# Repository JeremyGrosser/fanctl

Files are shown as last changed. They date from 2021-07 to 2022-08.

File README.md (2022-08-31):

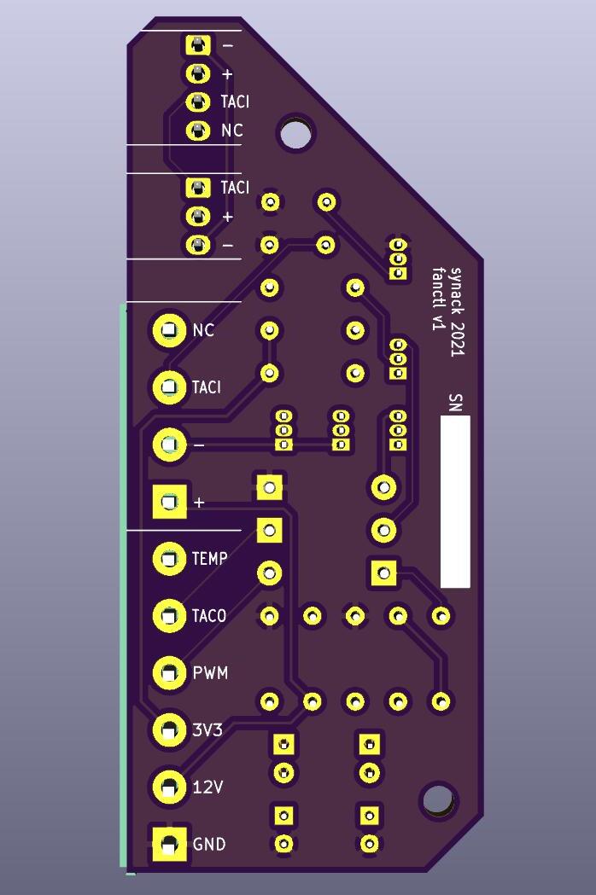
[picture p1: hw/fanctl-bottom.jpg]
PCB render


[Schematic](https://github.com/JeremyGrosser/fanctl/raw/master/hw/fanctl.pdf)

This project was meant to demonstrate closed loop PID control of a 3-pin PC
fan. While the resulting board works, I learned that the tachometer pin on the
fan is connected to a hall effect sensor, powered by +12V. This means that you
cannot sense and control the fan's speed at the same time. I came to the
conclusion that you should spend a few more dollars on a 4-pin fan that has an
onboard MOSFET and a separate signal for PWM.

I'm providing the the code and board files here as they may still be
interesting or useful as a reference or teaching tool.

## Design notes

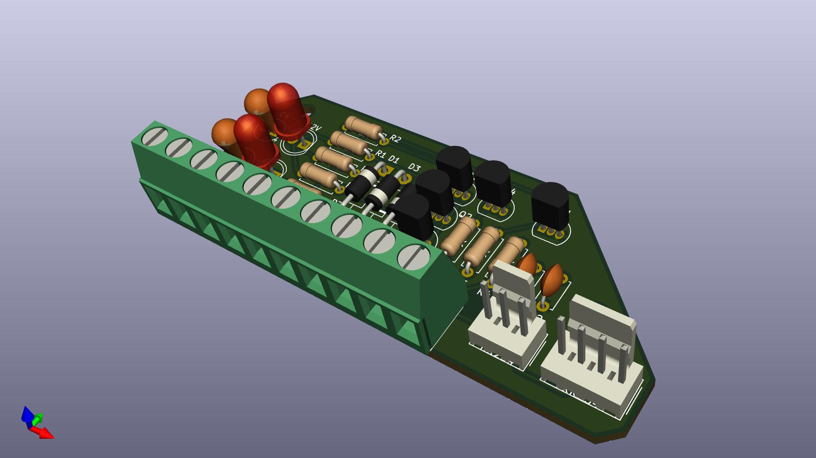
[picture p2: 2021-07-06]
hw/fanctl.jpg

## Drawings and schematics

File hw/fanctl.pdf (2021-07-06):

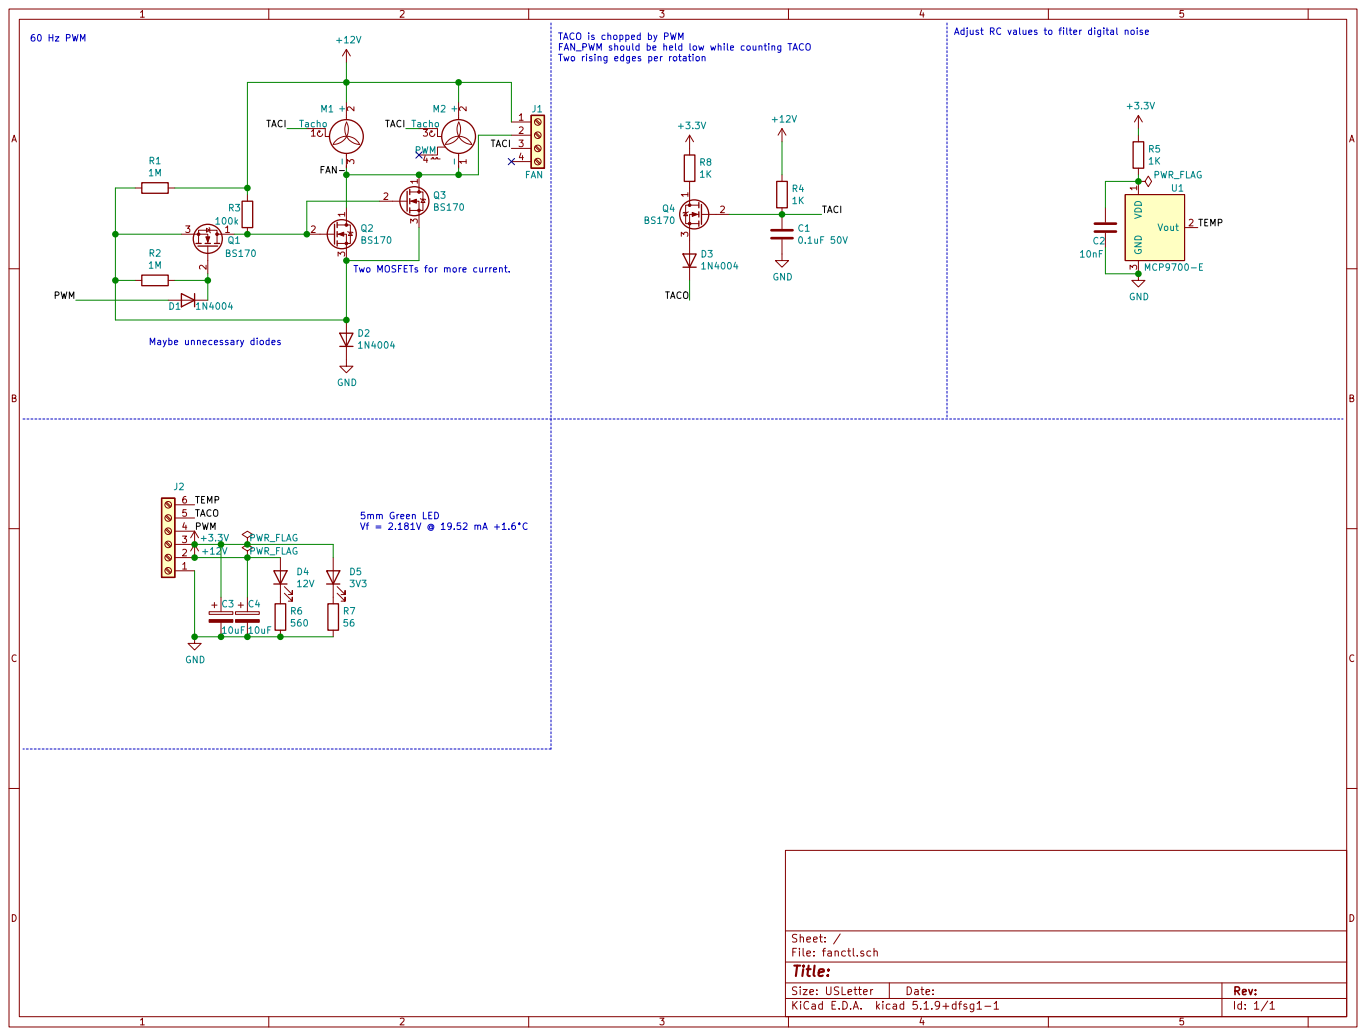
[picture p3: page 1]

Two rising edges per rotation Two MOSFETs for more current. Maybe unnecessary diodes

Adjust RC values to filter digital noise

FAN_PWM should be held low while counting TACO

2 | +12V | PWR_FLAG | 3V3 D4

Id: 1/1 Title: File: fanctl.sch Sheet: / R6

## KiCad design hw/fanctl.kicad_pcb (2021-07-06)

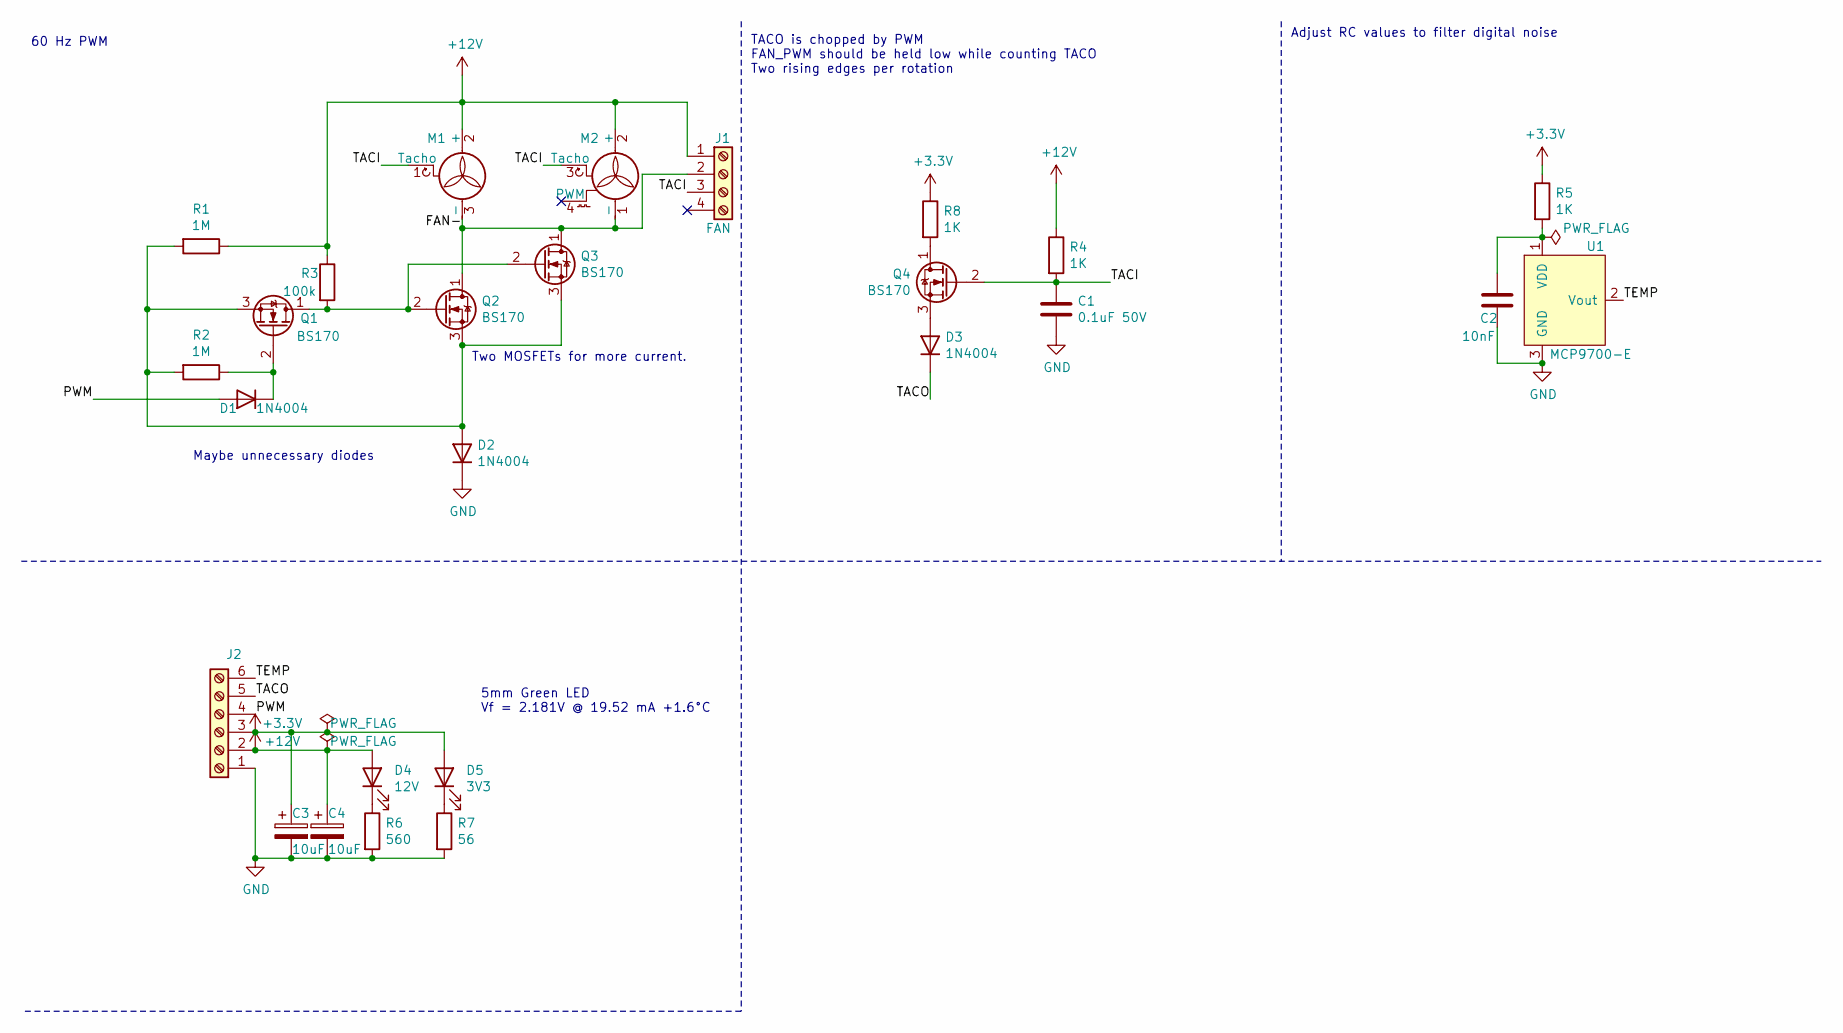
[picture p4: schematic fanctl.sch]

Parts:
C1: 0.1uF 50V; C_Disc_D4.7mm_W2.5mm_P5.00mm
C2: 10nF; C_Disc_D4.7mm_W2.5mm_P5.00mm
C3, C4: 10uF; CP_Radial_Tantal_D5.0mm_P2.50mm
D1, D2, D3: 1N4004; D_DO-41_SOD81_P10.16mm_Horizontal
D4: 12V; LED_D5.0mm
D5: 3V3; LED_D5.0mm
J1: FAN; TerminalBlock_bornier-4_P5.08mm
J2: Screw_Terminal_01x06; TerminalBlock_bornier-6_P5.08mm
M1: FAN; Molex_KK-254_AE-6410-03A_1x03_P2.54mm_Vertical
M2: FAN; Molex_KK-254_AE-6410-04A_1x04_P2.54mm_Vertical
Q1, Q2, Q3, Q4: BS170; TO-92_Inline
R1, R2: 1M; R_Axial_DIN0207_L6.3mm_D2.5mm_P7.62mm_Horizontal
R3: 100k; R_Axial_DIN0207_L6.3mm_D2.5mm_P7.62mm_Horizontal
R4, R5, R8: 1K; R_Axial_DIN0207_L6.3mm_D2.5mm_P7.62mm_Horizontal
R6: 560; R_Axial_DIN0207_L6.3mm_D2.5mm_P7.62mm_Horizontal
R7: 56; R_Axial_DIN0207_L6.3mm_D2.5mm_P7.62mm_Horizontal
U1: MCP9700-E; TO-92_Inline

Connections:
+3V3: C3.1, D5.2 (A), J2.3, R5.1, R8.1
+12V: C4.1, D4.2 (A), J1.1, J2.2, M1.2 (+), M2.2 (+), R1.1, R3.1, R4.1
/FAN-: J1.2, M1.3 (-), M2.1 (-), Q2.1 (D), Q3.1 (D)
/PWM: D1.2 (A), J2.4
/TACI: C1.1, J1.3, M1.1 (Tacho), M2.3 (Tacho), Q4.2 (G), R4.2
/TACO: D3.1 (K), J2.5
/TEMP: J2.6, U1.2 (Vout)
GND: C1.2, C2.2, C3.2, C4.2, D2.1 (K), J2.1, R6.2, R7.2, U1.3 (GND)
unnamed: C2.1, R5.2, U1.1 (VDD)
unnamed: D1.1 (K), Q1.2 (G), R2.1
unnamed: D2.2 (A), Q1.3 (S), Q2.3 (S), Q3.3 (S), R1.2, R2.2
unnamed: D3.2 (A), Q4.3 (S)
unnamed: D4.1 (K), R6.1
unnamed: D5.1 (K), R7.1
unnamed: Q1.1 (D), Q2.2 (G), Q3.2 (G), R3.2
unnamed: Q4.1 (D), R8.2

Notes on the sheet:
Two MOSFETs for more current.
Maybe unnecessary diodes
TACO is chopped by PWM FAN_PWM should be held low while counting TACO Two rising edges per rotation
Adjust RC values to filter digital noise
60 Hz PWM
5mm Green LED Vf = 2.181V @ 19.52 mA +1.6°C

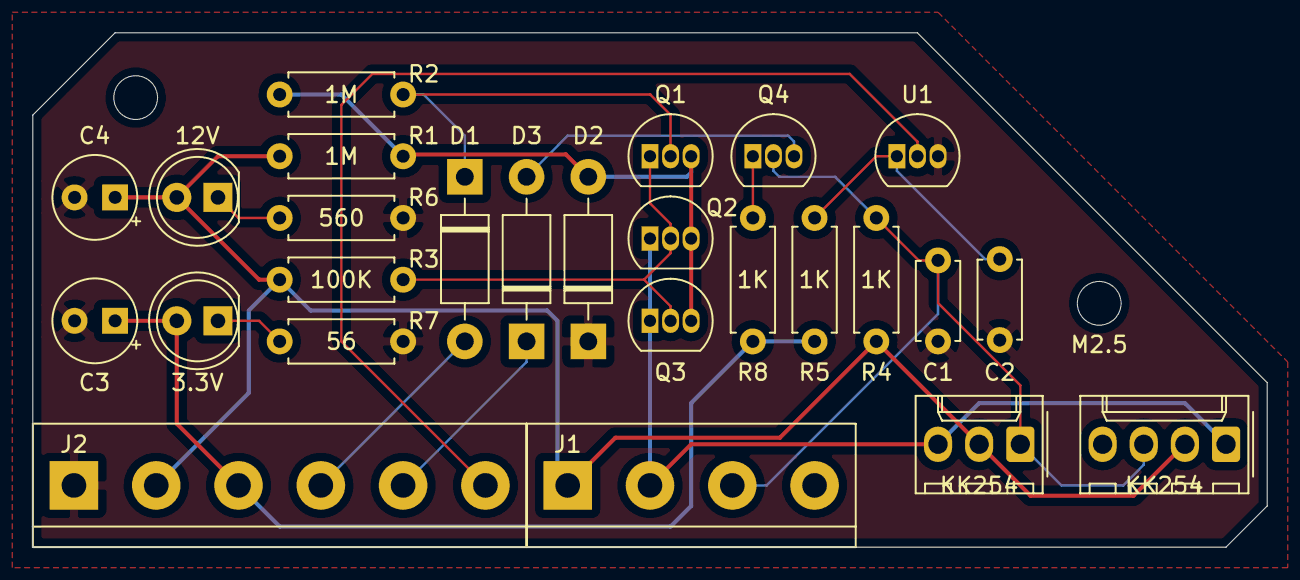
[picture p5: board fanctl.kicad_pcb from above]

Board: 2 copper layers, 76.2 x 31.8 mm, 27 parts (0 on the bottom side), 16 nets.

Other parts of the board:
M2.5: MountingHole_2.7mm_M2.5_ISO14580

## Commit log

2021-07-06 schematic drc
    [fanctl.sch]
2021-07-06 pcb layout
    [fanctl.sch]
2021-07-06 layout done
    [fanctl.kicad_pcb, fanctl.sch]
2021-07-06 schematic and silkscreen nits
    [fanctl.kicad_pcb, fanctl.sch]
2021-07-06 resize schematic for US Letter and generate PDF
    [fanctl.sch]
2021-07-11 fan servo
2021-07-16 pid control
2021-07-16 pid control sim
2021-07-16 pid tuning
2022-08-31 kicad 5.1
    [fanctl.kicad_pcb, fanctl.sch]
2022-08-31 add pcb render to readme
2022-08-31 crop pcb image
2022-08-31 Link to schematic
